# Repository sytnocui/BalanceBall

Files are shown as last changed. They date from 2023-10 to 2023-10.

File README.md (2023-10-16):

# 平衡立方体的球形版

**BalanceBall**

——by sytnocui 2023/8/31 v1.0

b站视频链接： TODO

## 0. 悲催往事

如果你打过**2021年的电赛**，你一定知道元器件清单里有一项是**亚克力球**，当时所有人都猜题目是球型机器人，一时间B站遍地都是球形机器人的视频，我们也为此屯了一堆的亚克力球，为了买球少说就花了200块钱。但可能因为疫情推迟比赛等原因，最后控制题却是一个和亚克力球毫无关系的医院物流小车。在我们破大防的同时，那一堆亚克力球怎么处理就成了问题。

>   亚克力球滞销，救救我们！！！
>

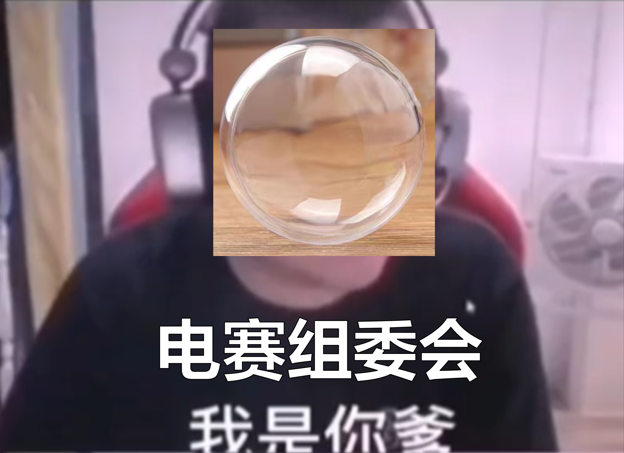
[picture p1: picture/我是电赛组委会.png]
我是电赛组委会


## 1. 项目说明

本项目旨在做出**球形版的平衡立方体**。在总体架构上，使用三个无刷电机带动三个正交安装的飞轮，并将整个球至于由三个**全向轮**构成的底盘上。全向轮允许前进方向和轴向的运动，则三个全向轮构成的底盘即可允许平衡球在上面做**三自由度全姿态自由机动**。球在全向轮底盘上，利用角动量守恒的原理实现球在底盘上的全姿态自由机动。

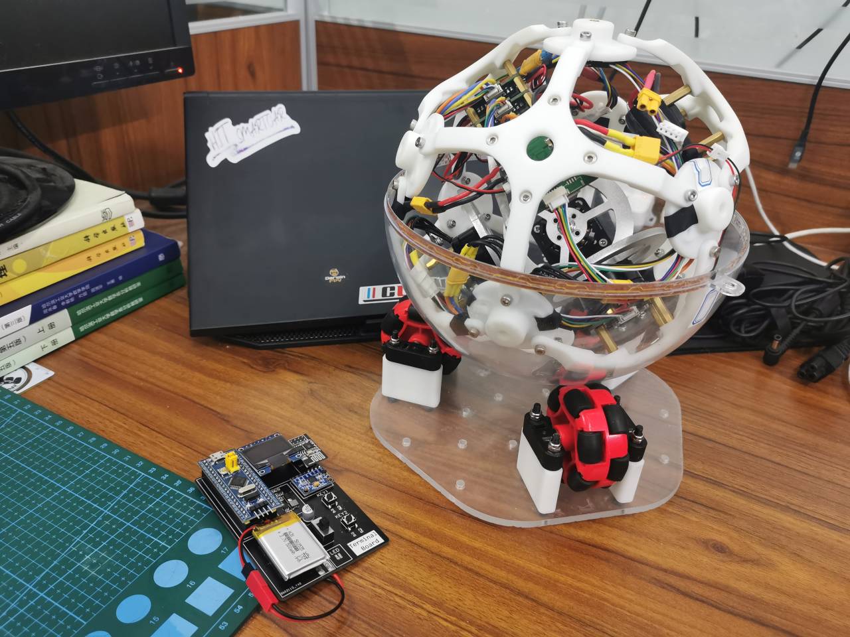
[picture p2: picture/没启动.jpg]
没启动


再贴张solidworks爆炸渲染图~

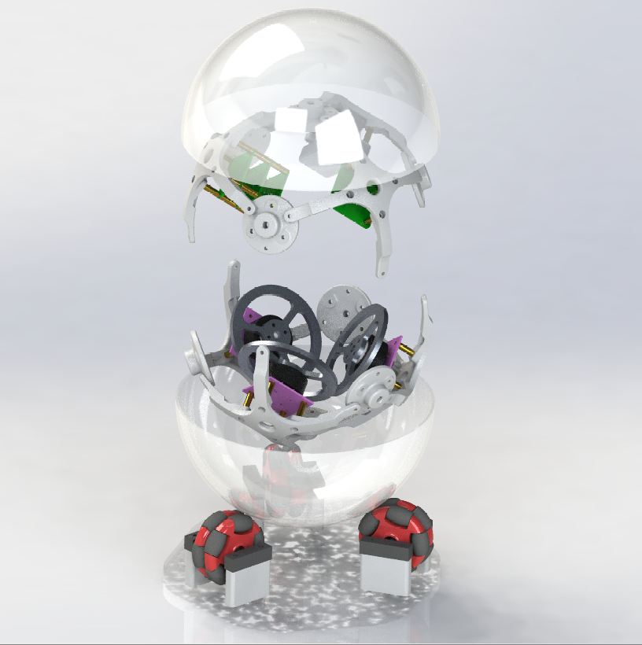
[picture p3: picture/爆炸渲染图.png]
爆炸渲染图


## 2. 开源协议

本项目使用 Apache 2.0 开源协议，转载请标明出处

## 3. 项目属性

本项目为首次公开，为本人原创项目。项目未曾在别的比赛中获奖。

另外，本项目同时也是我大四的大创项目，目前还未结题，之后会不会传给学弟去报竞赛还待商榷。

## 4. 项目相关功能及实物展示

-   平衡球全姿态自由转动

-   平衡球三轴角速度闭环控制与助力模式

-   平衡球三轴姿态跟踪随动，需搭配终端完成

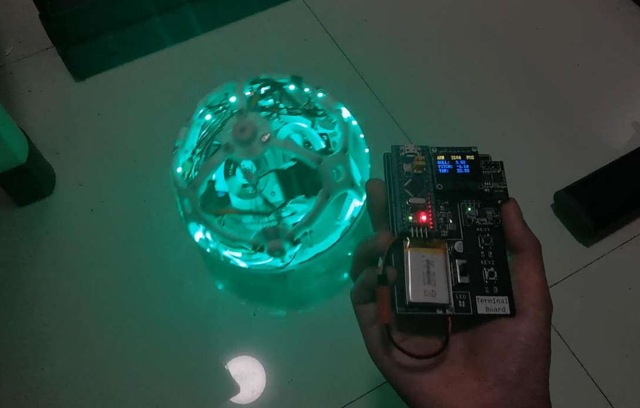
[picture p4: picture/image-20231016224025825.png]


-   平衡球实时发布自身三轴姿态，可模仿流浪地球方向盘，用于游玩各种赛车游戏

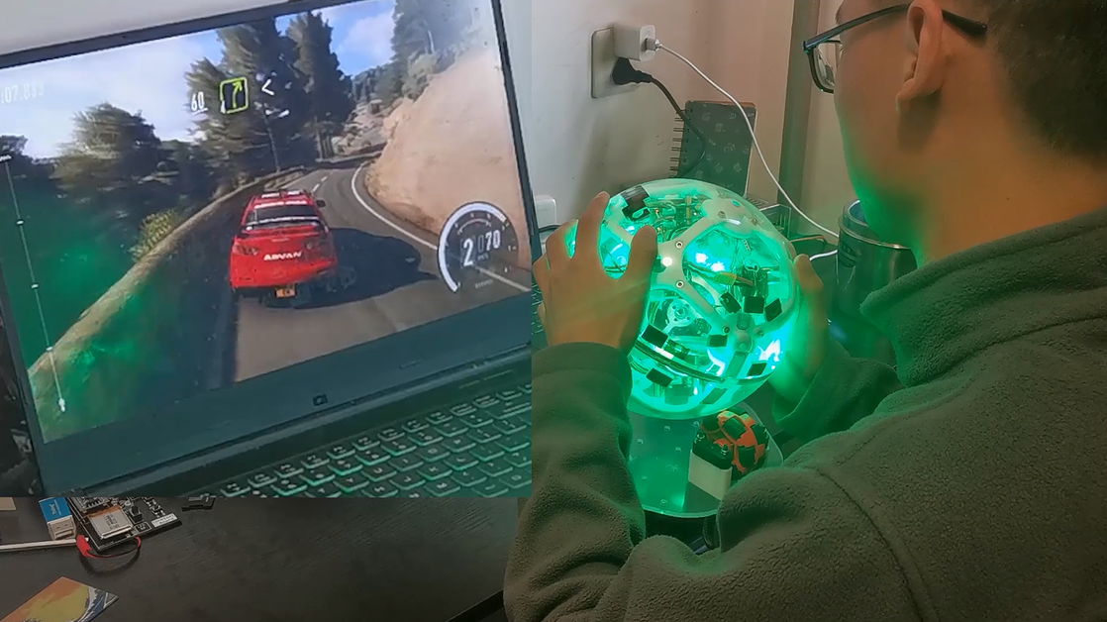
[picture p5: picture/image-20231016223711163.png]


## 5. 设计原理

项目总体可分为结构设计，硬件设计，软件设计三部分

### 5.1 结构设计

项目的结构设计理念很大程度上参考了苏黎世的经典平衡立方体：

平衡立方体视频

依照上图，平衡立方体有六个面，按照离地面的远近关系，咱们可以分成上三面和下三面。可以很明显得看到，平衡立方体的三个正交飞轮安装在下三面，而电池、电路板等均安装在上三面。

根据立体几何原理，可以很顺理成章地想到正方体是有外接球的。**取平衡立方体的外接球，将其六个面全部向外投影到其外接球上，就是咱们的平衡球**。

依据此建立的3D模型如下：

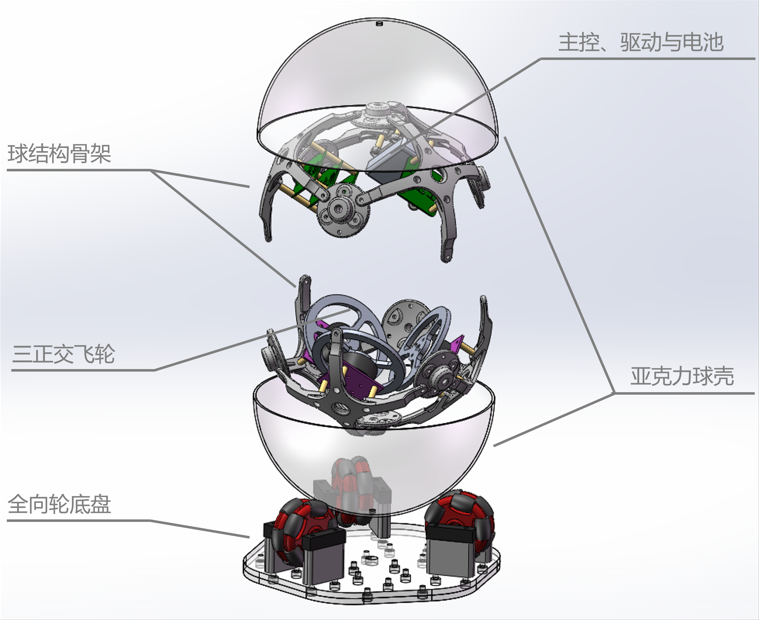
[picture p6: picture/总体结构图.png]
总体结构图


### 5.2 硬件设计

本项目设计有主控板，FOC驱动板，编码器板与陀螺仪板。项目硬件拓扑图如下：

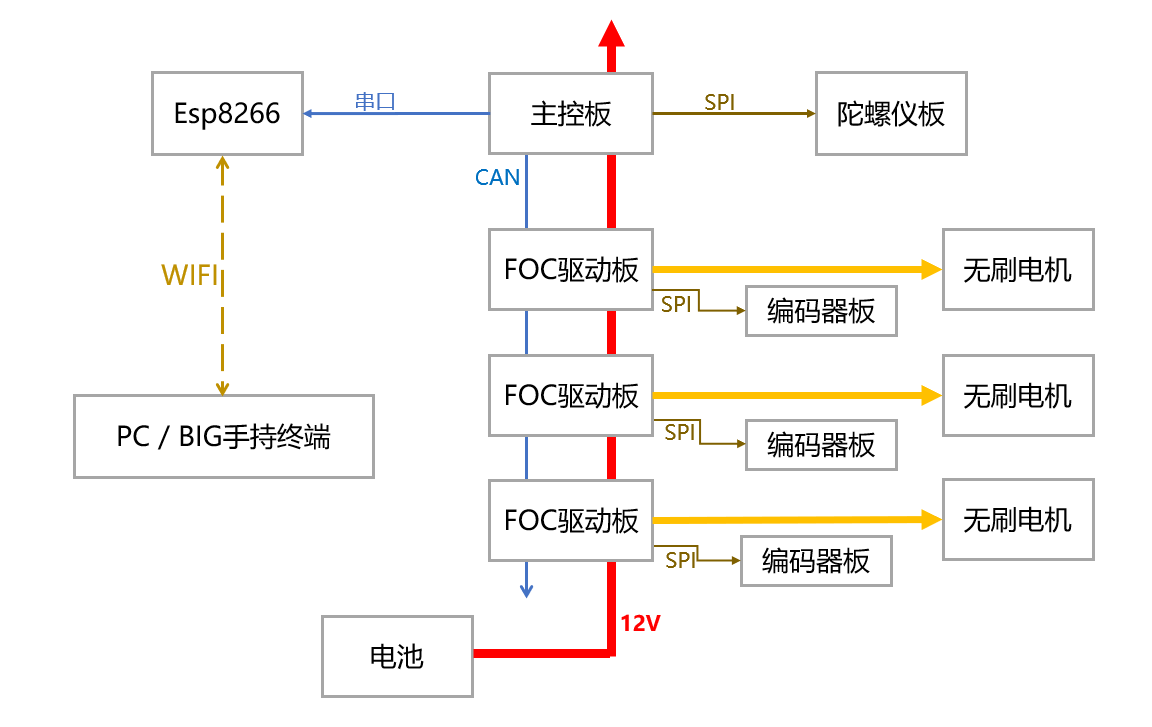
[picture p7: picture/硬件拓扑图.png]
硬件拓扑图


其中：

-   主控板和FOC驱动板全部采用级联方式供电，也通过CAN总线级联传递目标指令。
-   共三个FOC驱动板，每个FOC驱动板均连接一个编码器板获取无刷电机位置，并驱动一个无刷电机。
-   主控板连接有一块陀螺仪板，实时读取姿态信息。
-   主控板连接有一块esp8266通信模块

#### 5.2.1 主控板

主控板为四层板，可嘉立创免费打印。主要完成WIFI无线通信，读取陀螺仪姿态，姿态解算，控制模式管理，控制算法运行等。

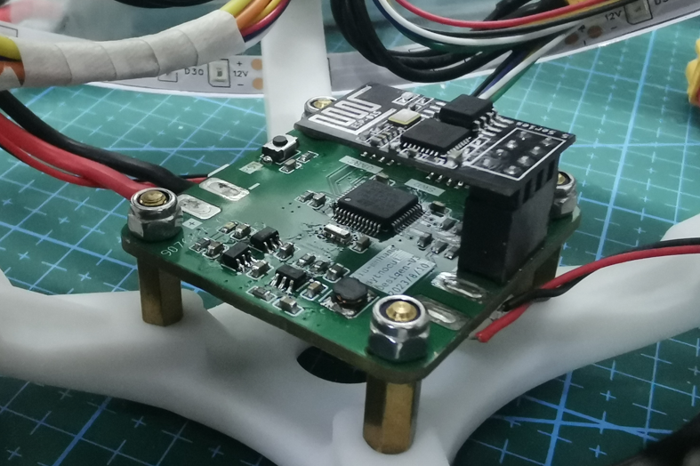
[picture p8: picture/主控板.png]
主控板


-   主控：STM32F103C8T6
-   晶振： 村田陶瓷三脚晶振CSTCE 8M （**稚晖君机械臂同款，不需要接负载电容**）

-   CAN通讯芯片：TJA1050T（**注意需5V供电，否则单片机CAN收发会卡死**）

-   电源管理：JW5026+ME6211
-   无线通信：经典插针式Esp8266无线通信模块

-   所用排座皆为GH1.25型号；

>   某宝上均可以买到，估测成本价一套下来大致30rmb左右（电子元件价格可能会有变化）。

配套编码器板可为：ICM20602，MPU6050，*ICM42688P（暂有问题，发热严重，请用icm20602模块代替）*

注意：编码器板使用热熔胶固定在球的内部最顶点，与地面平行。

#### 5.2.2 驱动板

驱动板为四层板，可嘉立创免费打印。驱动板主要完成FOC速度闭环驱动。

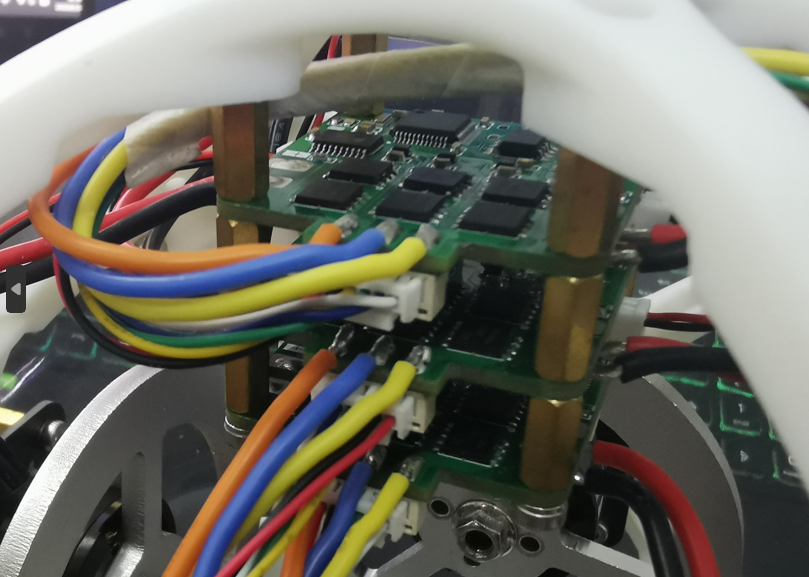
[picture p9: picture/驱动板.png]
驱动板


驱动板设计参考了柠檬FOC开源板，基于GD32进行设计。

参考地址： [【新春快乐】柠檬FOC开源板 - 嘉立创EDA开源硬件平台 (oshwhub.com)](https://oshwhub.com/a1804889557/xin-chun-kuai-le-ning-meng-FOCka) 

驱动板硬件部分自主设计，软件部分直接烧录柠檬FOC的代码使用。原开源项目可以通过putty串口助手设置电流闭环，速度和位置闭环模式，由于项目需要这里采用了速度阶跃变化模式。

使用原固件时注意在串口调试助手中修改电源欠压保护和速度保护参数，防止速度突变过快导致的电机停转。

驱动板参数如下：

-   主控：GD32C103CBT6
-   晶振： 村田陶瓷三脚晶振CSTCE 8M

-   CAN通讯芯片：SN65HVD232D

-   电源管理：JW5026+RT9013-3.3

-   电机驱动芯片：FD6288T （电机驱动芯片+mos管，大电流方案）

-   NMOS：TPH1R403NL

-   电流采样：LMV358IPWRG4 偏置低采

-   采样电阻：1206 1mR

-   所用排座皆为GH1.25型号

-   配套编码器：MT6816（**需要买支持SPI模式的**，很容易买错，不要买错了）

>   某宝上均可以买到，估测成本价一套下来大致60rmb左右（电子元件价格可能会有变化）。

#### 5.3.3 BIG手持终端

BIG手持终端是两层板，可嘉立创免费打印。BIG手持终端主要完成远程改变控制模式，安全管理，实时状态显示，发布目标位姿等功能。

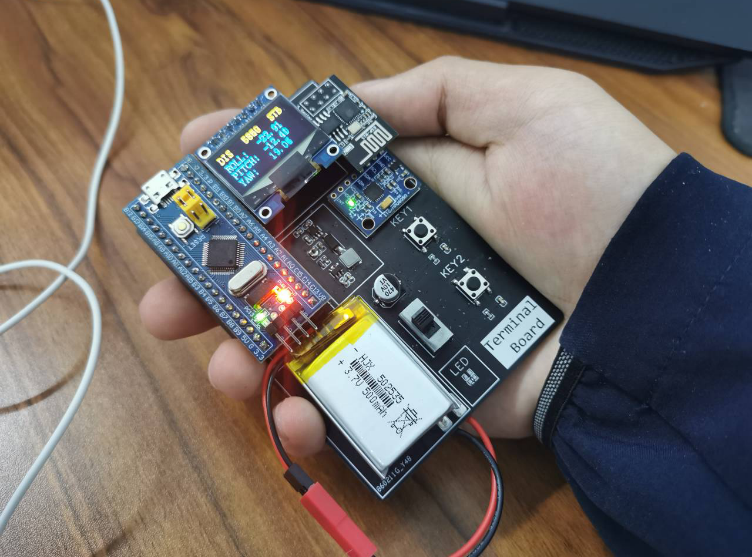
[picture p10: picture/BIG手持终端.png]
BIG手持终端


该模块对标稚晖君的PICO小终端设计，主要完成一些人机交互的功能。因为面向初学者，所有看起来比较粗野。因为PICO是微小的意思，稚晖君的PICO确实很小，但我这个手持终端却很大，所以起名叫**BIG**。

手持终端参数如下：

-   主控：STM32F103C8T6蓝宝石核心板
-   显示：7脚OLED显示屏，SPI模式

-   电池：1s锂电池 300mah 

-   陀螺仪：经典MPU6050模块

-   无线通信：经典插针式Esp8266无线通信模块

### 5.3 软件设计

#### 5.3.1 全姿态阻力效果

在主控板上进行，利用Mahony姿态解算方法，解出实时roll pitch yaw三轴角度，并分别建立PID反馈控制。每当有某个轴上有角速度，通过PID算法在该轴上产生相反方向的控制输出。最终将三轴的PID控制输出叠加后，左乘转速分配矩阵，将其解算成三个正交安装的飞轮的转速，输出给FOC驱动板，即可在球的三自由度全姿态运动中产生阻力效果。

#### 5.3.2 三轴姿态跟踪随动

在5.3.1节的基础上，添加姿态角反馈，由BIG手持终端收集自身姿态，作为平衡球姿态的目标值，与平衡球姿态的实际值做差，构成PID控制器。最终实现三轴姿态跟踪随动。

因为全向轮底盘会给系统引入非常大的摩擦力，所以目前这个功能需要将球直接放在地面上，而不能放在全向轮底盘上进行。

考虑到纯PID效果有限，本项目之后会使用LQR等控制算法部署上做进一步对比测试。

#### 5.3.3 作为方向盘游玩赛车游戏

我们偶然发现，我们的球和流浪地球的球形方向盘非常类似，于是，使用wifi模块连接电脑，接收球形仿真器实时姿态信息，并将其使用python的vgamepad库，映射成虚拟的xbox游戏手柄的摇杆值（方向盘，油门，刹车等）。这样就可以在尘埃拉力赛2.0等赛车游戏中识别虚拟游戏摇杆，进而获得控制数据了。

因为是将控制数据封装成xbox手柄的形式，所以不管游玩任何赛车游戏，都不会有兼容性的问题。

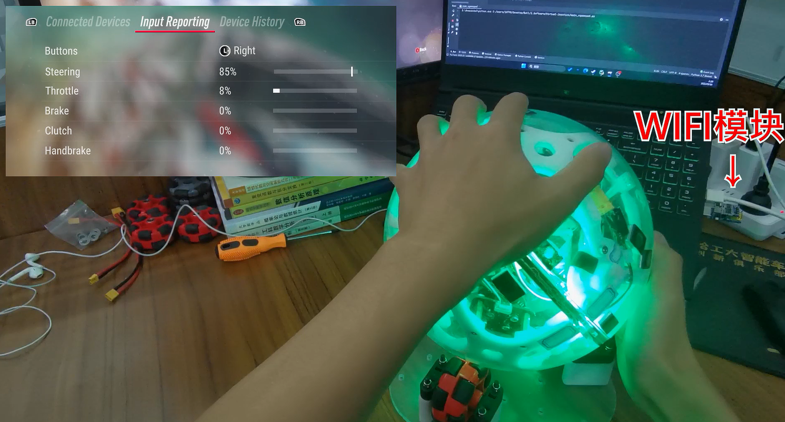
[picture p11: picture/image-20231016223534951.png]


## 6. 注意事项

### 6.1 软件说明

本项目提供主控板与BIG手持终端的固件代码，驱动板的固件与柠檬FOC完全一致，烧录与使用也请完全参考柠檬FOC的工程：

参考链接： [【新春快乐】柠檬FOC开源板 - 嘉立创EDA开源硬件平台 (oshwhub.com)](https://oshwhub.com/a1804889557/xin-chun-kuai-le-ning-meng-FOCka) 

本项目所有单片机固件均使用Clion开发，如果你对Clion工程配置比较生疏，建议观看稚晖君的Clion+Stm32环境配置指南：

参考链接： [配置CLion用于STM32开发【优雅の嵌入式开发】 - 知乎 (zhihu.com)](https://zhuanlan.zhihu.com/p/145801160) 

### 6.2 电机选型

飞轮与无刷电机的选型是十分重要的，由于整个系统摩擦力很大，开源社区常见的莱洛三角形和平衡方块使用的低kv云台电机很难满足力矩需求。我在淘宝二手电机无意中发现了这款电机：

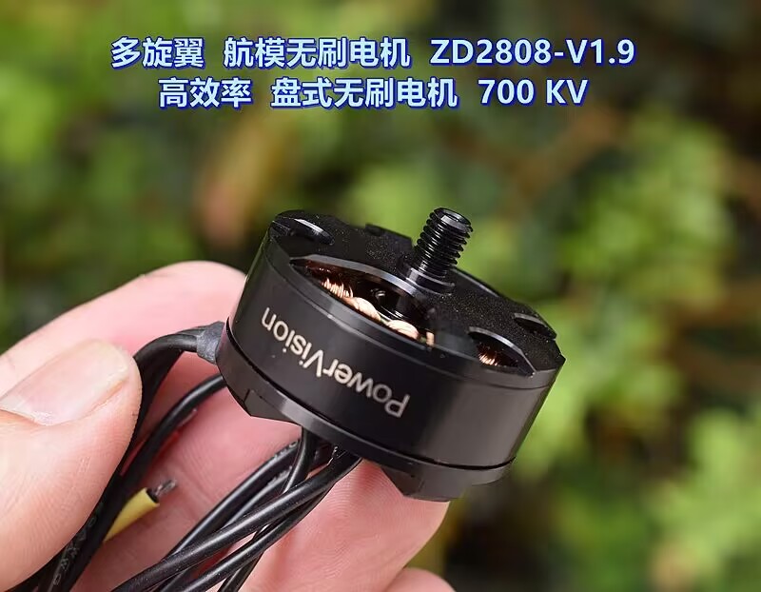
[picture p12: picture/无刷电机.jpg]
无刷电机


经过测试，该电机负载能力用到本项目非常合适，成本低廉（仅16元），且比较节省空间。考虑到这种二手电机经常卖完就没了，如果之后该电机售罄，可以考虑使用 *大疆2312精灵电机* 替代。

另外，若铝合金飞轮可以提供的反作用力矩不足，可模仿这个开源工程的方案，自制飞轮并在外边缘钻孔安装螺栓来增加飞轮转动惯量。

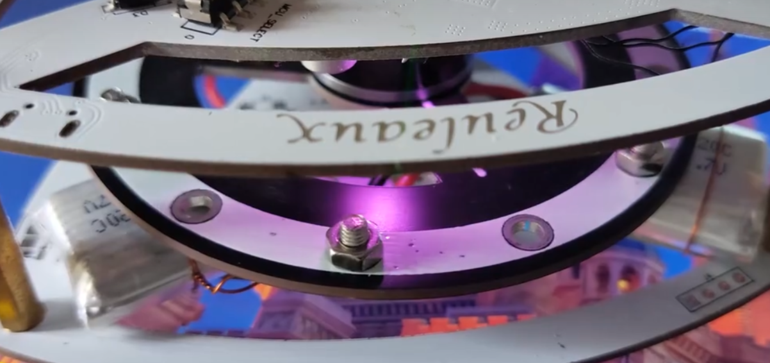
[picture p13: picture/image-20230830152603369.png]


参考地址：[基于LQR控制器的自平衡莱洛三角形_哔哩哔哩_bilibili](https://www.bilibili.com/video/BV19v411n7mN/?vd_source=4ff5d8b280178b24895437b1b8ffd97e) 

### 6.3 陀螺仪选型

本项目涉及的陀螺仪板使用的是icm42688p，但是从某宝买的不同批次的icm42688p均出现虽然能读出正确的数据，但有发热严重（约60度），带来的温漂严重等问题。确认不是焊接问题，暂时不知道是不是物料问题或者硬件设计有问题。建议谨慎考虑从淘宝购买icm42688p。本项目暂时使用逐飞科技的icm20602模块充当陀螺仪板。

本项目目前使用的是从社团嫖的icm20602模块，同时球主控板也支持mpu6050接插件。三款陀螺仪的驱动代码均在工程中，但接口代码需自行更改。

## 8. 项目进度

**2023/8/30首次开源**

项目已完成的部分：

-   项目已完成所有结构+硬件设计与搭建，结构与硬件设计已经收敛成熟。
-   项目已完成所有逻辑代码编写。
-   项目已完成基础的控制算法的编写，可以完成基础的角速度闭环与姿态闭环控制。

项目的后续计划：

-   由于控制系统的复杂性，项目后续需要对姿态闭环控制代码做优化，主要措施包括：
    -   增加配重，使重心趋于球形正中心，且使三轴惯量趋于一致。
    -   PID是真不行，换成基于模型的控制算法，如基于欧拉方程基于LQR建模
    -   对摩擦力进行参数辨识，使用干扰观测器补偿之（也可使用ADRC算法）
    -   尝试基于四元数的姿态闭环控制，以消除欧拉角死锁问题。
-   项目成员正在自主研发基于stm32f103c8t6的FOC驱动代码。研发完成后将会替换掉目前使用的柠檬FOC大佬的基于gd32的驱动板。
-   将会基于Qt与OpenGL写一个能实时可视化姿态与远程调参的上位机软件，效果可参考稚晖君的电子机器人和各种飞控调试助手。
-   将会实现一套嵌入式shell，以支持通过wifi串口进行远程调参
-   为陀螺仪添加减震垫，防止电机的高频振动给陀螺仪引入干扰
-   找出icm42688p的问题，换掉现在正在用的icm20602

## 9. 物资说明

结构件物料清单：

| 物资 | 用途 | 需求个数 | 购买链接 |
| :--- | --- | :---: | --- |
| **球主体结构** | | | |
| 亚克力球壳 20mm | 球透明外壳 | >=2 | https://m.tb.cn/h.54hODsa?tk=Q7ZXdzW9Ydo |
| 3D打印（内部支撑架-连点） | 十字形主体框架 | 6 | 嘉立创三维猴 |
| 3D打印（内部支撑架-桥接点） | 主体框架的连接点 | 8 | 嘉立创三维猴 |
| 3D打印（支架-电池小） | 固定电池 | 1 | 嘉立创三维猴 |
| **无刷电机相关** | | | |
| 盘式无刷电机ZD2808-V1.9 | | 3 | https://m.tb.cn/h.5WJTsy4?tk=4qczdC51605 |
| 铝合金飞轮6mm 80mm | | 3 | https://m.tb.cn/h.5e1xS1N?tk=HlGCdC6gCA1 |
| 径向磁铁6*2.5 | 获取电机轴位置 | 3 | https://m.tb.cn/h.54hiYKJ?tk=QM5mdzWTh2m |
| 3M超能胶 | 将磁体固定在电机轴上 | 1 | https://m.tb.cn/h.54AlcCb?tk=jlEVdzWQEFG |
| **球主体配件** | | | |
| M3*8杯头螺丝 | 主要结构固定螺丝 | 若干 | |
| M3防松螺母 | 主要结构固定螺母 | 若干 | |
| 铜柱 M3*10+6 | 主要支撑铜柱 | 20 | |
| M3*5\*5嵌入式螺母 | 连接球壳与3D打印件 | 2 | |
| M3*8沉头螺丝 | 连接球壳与3D打印件 | 2 | |
| 配重 | 平衡重心位置 | 若干 | https://m.tb.cn/h.56VXPSI?tk=n4DUWYhMTac |
| **电路部分** | | | |
| 主控板 | | 1 | 嘉立创免费打板，元件自行处理 |
| FOC驱动板 | | 3 | 嘉立创免费打板，元件自行处理 |
| 编码器板 | | 3 | 嘉立创免费打板，元件自行处理 |
| 陀螺仪板（可选） | | 1 | 嘉立创免费打板，元件自行处理 |
| BIG手持终端 | | 1 | 嘉立创免费打板，元件自行处理 |
| wifi模块 | 球与BIG，球与PC通信  | 3 | https://m.tb.cn/h.56vZKps?tk=XmldWYhGjPn |
| wifi模块连接电脑的usb转串模块 | 球与PC通信 | 1 | https://m.tb.cn/h.56vZKps?tk=XmldWYhGjPn |
| 航模电池3s 550mah 85c | 供电 | >=1 | https://m.tb.cn/h.5fuIsF0?tk=Pxn2dzWQvsg |
| **线材** | | | |
| 硅胶线18awg | 电源线 | 若干 | |
| 硅胶线20awg | 电机线 | 若干 | |
| GH1.25 6p 双头反向 30cm | 编码器线 | 3 | |
| GH1.25 6p 双头反向 30cm | 陀螺仪线 | 1 | |
| GH1.25 2p 双头反向 15cm | CAN总线 | 4 | |
| xt30头 | 连接电池 | 1 | |
| **底盘** | | | |
| 亚克力切割（底盘-上层） | 底盘主体 | 1 | 淘宝找亚克力切割 |
| 3D打印（全向轮轴座-键） | 支撑全向轮 | 3 | 嘉立创三维猴 |
| 3D打印（全向轮轴座-圆） | 支撑全向轮 | 3 | 嘉立创三维猴 |
| 3D打印（万向轮支撑腿-分体式） | 支撑全向轮 | 6 | 嘉立创三维猴 |
| F车模全向轮 | 支撑亚克力球壳 | 3 | https://m.tb.cn/h.5Vqiebu?tk=y4CAdzW76o4 |
| 轴承7\*11\*3 | 连接全向轮和光轴 | 6 | https://m.tb.cn/h.54hQEqA?tk=cFWBdzW7L1a |
| 光轴切割（全向轮光轴） | 支撑全向轮，注意开槽 | 3 | https://m.tb.cn/h.5fuKVfU?tk=G4sGdzW7mtl |
| M4*55螺丝 | 固定全向轮轴座 | 12 | |
| M4防松螺母 | 固定全向轮轴座 | 12 | |
| 脚垫（可选） | 底座防滑 | 若干 | https://m.tb.cn/h.54AknHL?tk=cSfIdzWjeUe |

整套下来价格800~1000元左右，某些零部件价格变化较大，请以实际情况为准。

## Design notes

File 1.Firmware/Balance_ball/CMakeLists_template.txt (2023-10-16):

#THIS FILE IS AUTO GENERATED FROM THE TEMPLATE! DO NOT CHANGE!
set(CMAKE_SYSTEM_NAME Generic)
set(CMAKE_SYSTEM_VERSION 1)
cmake_minimum_required(VERSION 3.17)

# specify cross compilers and tools
set(CMAKE_C_COMPILER arm-none-eabi-gcc)
set(CMAKE_CXX_COMPILER arm-none-eabi-g++)
set(CMAKE_ASM_COMPILER  arm-none-eabi-gcc)
set(CMAKE_AR arm-none-eabi-ar)
set(CMAKE_OBJCOPY arm-none-eabi-objcopy)
set(CMAKE_OBJDUMP arm-none-eabi-objdump)
set(SIZE arm-none-eabi-size)
set(CMAKE_TRY_COMPILE_TARGET_TYPE STATIC_LIBRARY)

# project settings
project(BalanceBall C CXX ASM)
set(CMAKE_CXX_STANDARD 17)
set(CMAKE_C_STANDARD 11)

#Uncomment for hardware floating point
#add_compile_definitions(ARM_MATH_CM4;ARM_MATH_MATRIX_CHECK;ARM_MATH_ROUNDING)
#add_compile_options(-mfloat-abi=hard -mfpu=fpv4-sp-d16)
#add_link_options(-mfloat-abi=hard -mfpu=fpv4-sp-d16)

#Uncomment for software floating point
#add_compile_options(-mfloat-abi=soft)

add_compile_options(-mcpu=cortex-m3 -mthumb -mthumb-interwork)
add_compile_options(-ffunction-sections -fdata-sections -fno-common -fmessage-length=0)

# uncomment to mitigate c++17 absolute addresses warnings
#set(CMAKE_CXX_FLAGS "${CMAKE_CXX_FLAGS} -Wno-register")

if ("${CMAKE_BUILD_TYPE}" STREQUAL "Release")
    message(STATUS "Maximum optimization for speed")
    add_compile_options(-Ofast)
elseif ("${CMAKE_BUILD_TYPE}" STREQUAL "RelWithDebInfo")
    message(STATUS "Maximum optimization for speed, debug info included")
    add_compile_options(-Ofast -g)
elseif ("${CMAKE_BUILD_TYPE}" STREQUAL "MinSizeRel")
    message(STATUS "Maximum optimization for size")
    add_compile_options(-Os)
else ()
    message(STATUS "Minimal optimization, debug info included")
    add_compile_options(-Og -g)
endif ()

include_directories(
        Core/Inc
        USB_DEVICE/App
        USB_DEVICE/Target
        Drivers/STM32F1xx_HAL_Driver/Inc
        Drivers/STM32F1xx_HAL_Driver/Inc/Legacy
        Middlewares/ST/STM32_USB_Device_Library/Core/Inc
        Middlewares/ST/STM32_USB_Device_Library/Class/CDC/Inc
        Drivers/CMSIS/Device/ST/STM32F1xx/Include
        Drivers/CMSIS/Include
        Bsp
        Ctrl
        UserApp
)

add_definitions(-DUSE_HAL_DRIVER -DSTM32F103xB)

file(GLOB_RECURSE SOURCES
        "startup/*.*"
        "Middlewares/*.*"
        "Drivers/*.*"
        "USB_DEVICE/*.*"
        "Core/*.*"
        "Ctrl/*.*"
        "Bsp/*.*"
        "UserApp/*.*"
        )

set(LINKER_SCRIPT ${CMAKE_SOURCE_DIR}/STM32F103C8Tx_FLASH.ld)

add_link_options(-Wl,-gc-sections,--print-memory-usage,-Map=${PROJECT_BINARY_DIR}/${PROJECT_NAME}.map)
add_link_options(-mcpu=cortex-m3 -mthumb -mthumb-interwork)
add_link_options(-T ${LINKER_SCRIPT})

add_executable(${PROJECT_NAME}.elf ${SOURCES} ${LINKER_SCRIPT})

set(HEX_FILE ${PROJECT_BINARY_DIR}/${PROJECT_NAME}.hex)
set(BIN_FILE ${PROJECT_BINARY_DIR}/${PROJECT_NAME}.bin)

add_custom_command(TARGET ${PROJECT_NAME}.elf POST_BUILD
        COMMAND ${CMAKE_OBJCOPY} -Oihex $<TARGET_FILE:${PROJECT_NAME}.elf> ${HEX_FILE}
        COMMAND ${CMAKE_OBJCOPY} -Obinary $<TARGET_FILE:${PROJECT_NAME}.elf> ${BIN_FILE}
        COMMENT "Building ${HEX_FILE}
Building ${BIN_FILE}")

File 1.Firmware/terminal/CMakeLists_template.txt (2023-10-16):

#THIS FILE IS AUTO GENERATED FROM THE TEMPLATE! DO NOT CHANGE!
set(CMAKE_SYSTEM_NAME Generic)
set(CMAKE_SYSTEM_VERSION 1)
cmake_minimum_required(VERSION 3.17)

# specify cross compilers and tools
set(CMAKE_C_COMPILER arm-none-eabi-gcc)
set(CMAKE_CXX_COMPILER arm-none-eabi-g++)
set(CMAKE_ASM_COMPILER  arm-none-eabi-gcc)
set(CMAKE_AR arm-none-eabi-ar)
set(CMAKE_OBJCOPY arm-none-eabi-objcopy)
set(CMAKE_OBJDUMP arm-none-eabi-objdump)
set(SIZE arm-none-eabi-size)
set(CMAKE_TRY_COMPILE_TARGET_TYPE STATIC_LIBRARY)

# project settings
project(terminal C CXX ASM)
set(CMAKE_CXX_STANDARD 17)
set(CMAKE_C_STANDARD 11)

#Uncomment for hardware floating point
#add_compile_definitions(ARM_MATH_CM4;ARM_MATH_MATRIX_CHECK;ARM_MATH_ROUNDING)
#add_compile_options(-mfloat-abi=hard -mfpu=fpv4-sp-d16)
#add_link_options(-mfloat-abi=hard -mfpu=fpv4-sp-d16)

#Uncomment for software floating point
#add_compile_options(-mfloat-abi=soft)

add_compile_options(-mcpu=cortex-m3 -mthumb -mthumb-interwork)
add_compile_options(-ffunction-sections -fdata-sections -fno-common -fmessage-length=0)

# uncomment to mitigate c++17 absolute addresses warnings
#set(CMAKE_CXX_FLAGS "${CMAKE_CXX_FLAGS} -Wno-register")

if ("${CMAKE_BUILD_TYPE}" STREQUAL "Release")
    message(STATUS "Maximum optimization for speed")
    add_compile_options(-Ofast)
elseif ("${CMAKE_BUILD_TYPE}" STREQUAL "RelWithDebInfo")
    message(STATUS "Maximum optimization for speed, debug info included")
    add_compile_options(-Ofast -g)
elseif ("${CMAKE_BUILD_TYPE}" STREQUAL "MinSizeRel")
    message(STATUS "Maximum optimization for size")
    add_compile_options(-Os)
else ()
    message(STATUS "Minimal optimization, debug info included")
    add_compile_options(-Og -g)
endif ()

include_directories(
        Core/Inc
        Drivers/STM32F1xx_HAL_Driver/Inc
        Drivers/STM32F1xx_HAL_Driver/Inc/Legacy
        Drivers/CMSIS/Device/ST/STM32F1xx/Include
        Drivers/CMSIS/Include
        Middlewares/ST/STM32_USB_Device_Library/Core/Inc
        Middlewares/ST/STM32_USB_Device_Library/Class/CDC/Inc
        USB_DEVICE/App
        USB_DEVICE/Target/
        Bsp
        UserApp
        Ctrl
)

add_definitions(-DUSE_HAL_DRIVER -DSTM32F103xB)

file(GLOB_RECURSE SOURCES "startup/*.*" "Drivers/*.*" "Core/*.*" "Bsp/*.*" "UserApp/*.*" "USB_DEVICE/*.*" "Middlewares/*.*"
        "Ctrl/*.*")

set(LINKER_SCRIPT ${CMAKE_SOURCE_DIR}/STM32F103C8Tx_FLASH.ld)

add_link_options(-Wl,-gc-sections,--print-memory-usage,-Map=${PROJECT_BINARY_DIR}/${PROJECT_NAME}.map)
add_link_options(-mcpu=cortex-m3 -mthumb -mthumb-interwork)
add_link_options(-T ${LINKER_SCRIPT})

add_executable(${PROJECT_NAME}.elf ${SOURCES} ${LINKER_SCRIPT})

set(HEX_FILE ${PROJECT_BINARY_DIR}/${PROJECT_NAME}.hex)
set(BIN_FILE ${PROJECT_BINARY_DIR}/${PROJECT_NAME}.bin)

add_custom_command(TARGET ${PROJECT_NAME}.elf POST_BUILD
        COMMAND ${CMAKE_OBJCOPY} -Oihex $<TARGET_FILE:${PROJECT_NAME}.elf> ${HEX_FILE}
        COMMAND ${CMAKE_OBJCOPY} -Obinary $<TARGET_FILE:${PROJECT_NAME}.elf> ${BIN_FILE}
        COMMENT "Building ${HEX_FILE}
Building ${BIN_FILE}")

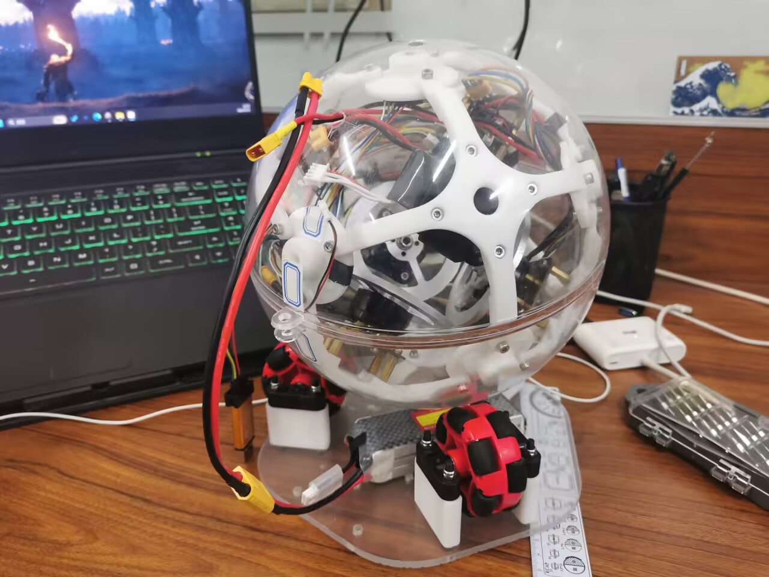
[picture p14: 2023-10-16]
picture/外接电池.jpg

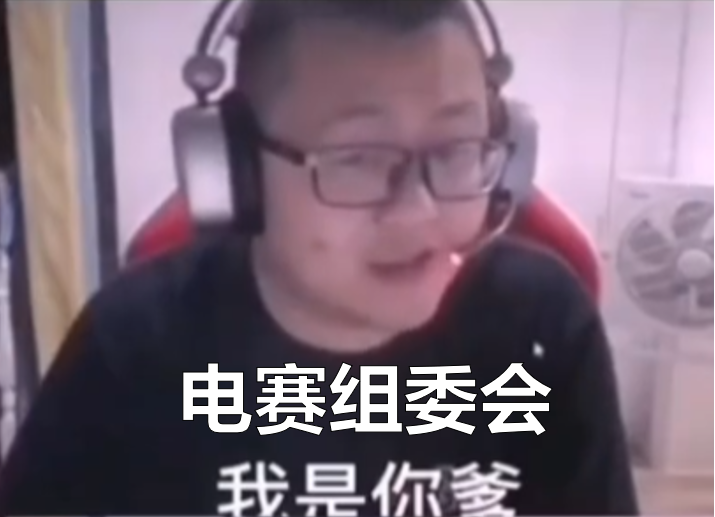
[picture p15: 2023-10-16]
picture/我是你爹.png

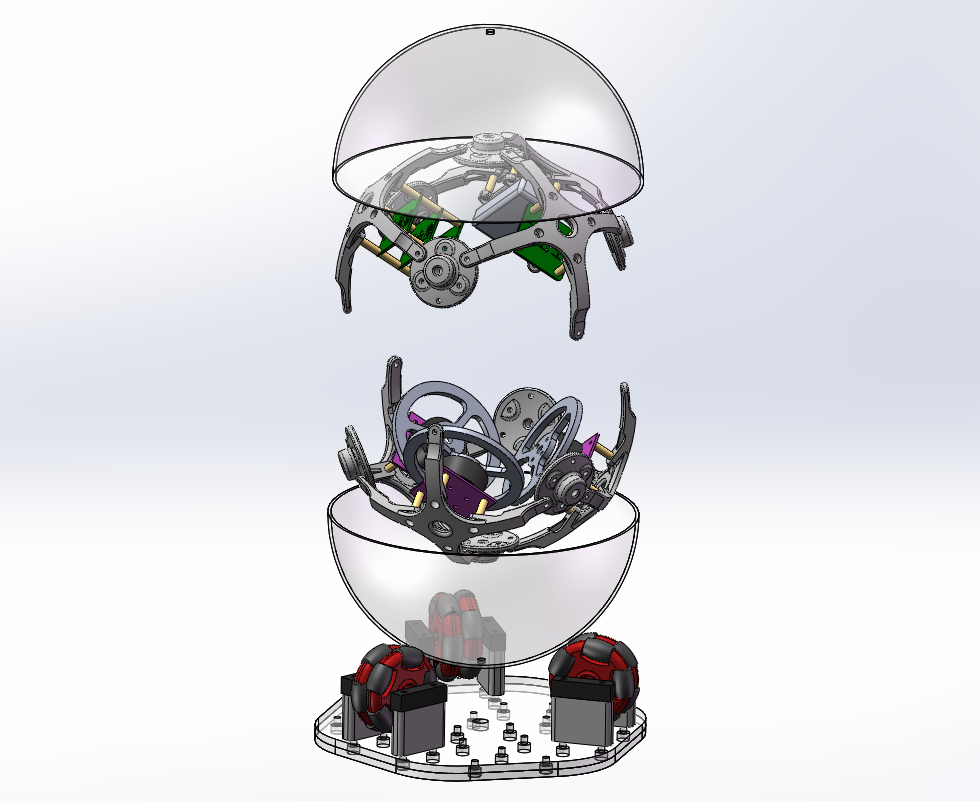
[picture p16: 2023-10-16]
picture/爆炸模型图.png

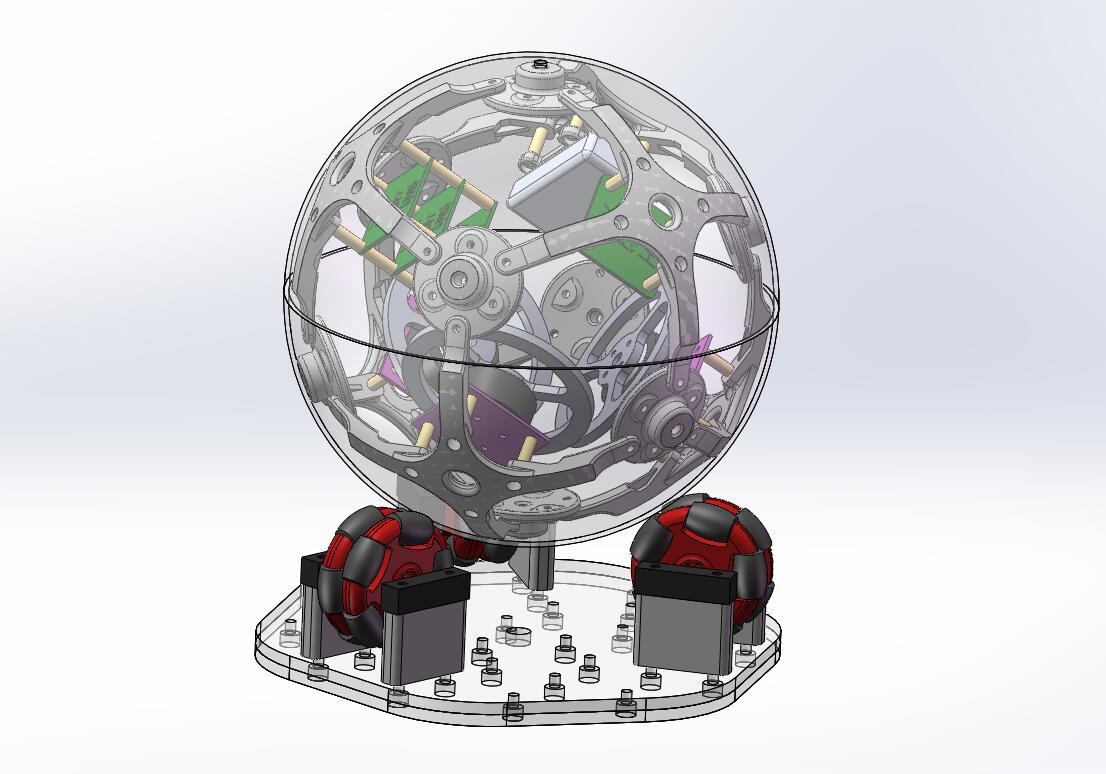
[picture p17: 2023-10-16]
picture/模型图.jpg

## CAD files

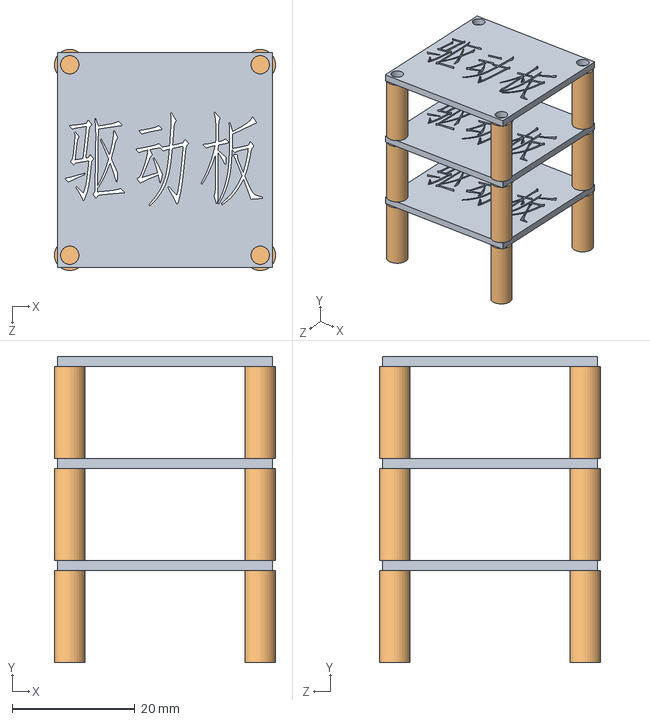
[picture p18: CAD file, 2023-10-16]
0.Model/装配体-驱动板.SLDASM
36.0 x 49.8 x 36.0 mm
驱动板 x 3
m3铜柱-主控板 x 12

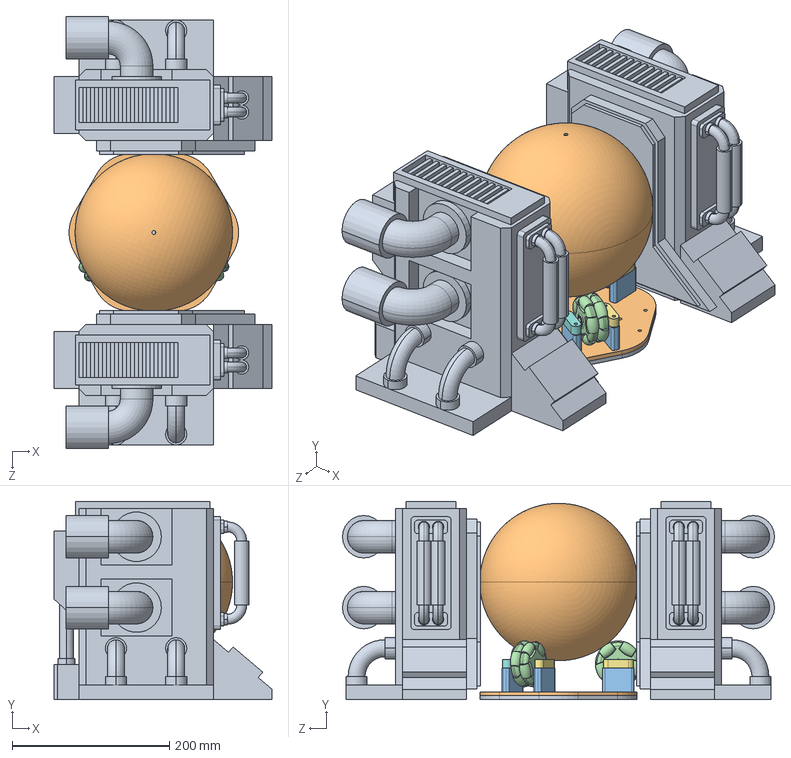
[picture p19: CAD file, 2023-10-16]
0.Model/整活/电厂装配体.SLDASM
277.0 x 252.0 x 549.0 mm
苏联电厂
底盘-上层
万向轮支撑腿-分体式 x 6
全向轮-网上找的模型58mm x 3
全向轮光轴 x 3
全向轮轴承 x 6
全向轮轴座-键 x 3
全向轮轴座-圆 x 3
底盘-下层
内部支撑架-连点 x 6
内部支撑架-桥接点 x 8
m3铜柱-4mm x 12
编码器板-AS5047P x 3
电机-2804 x 3
飞轮-80mm x 3
电机轴 x 3
m3铜柱-15mm x 12
半球壳-直径200 x 2
m3铜柱-电池 x 4
支架-电池小
电池-550mah
驱动板 x 3
m3铜柱-主控板 x 16
主控板
编码器板

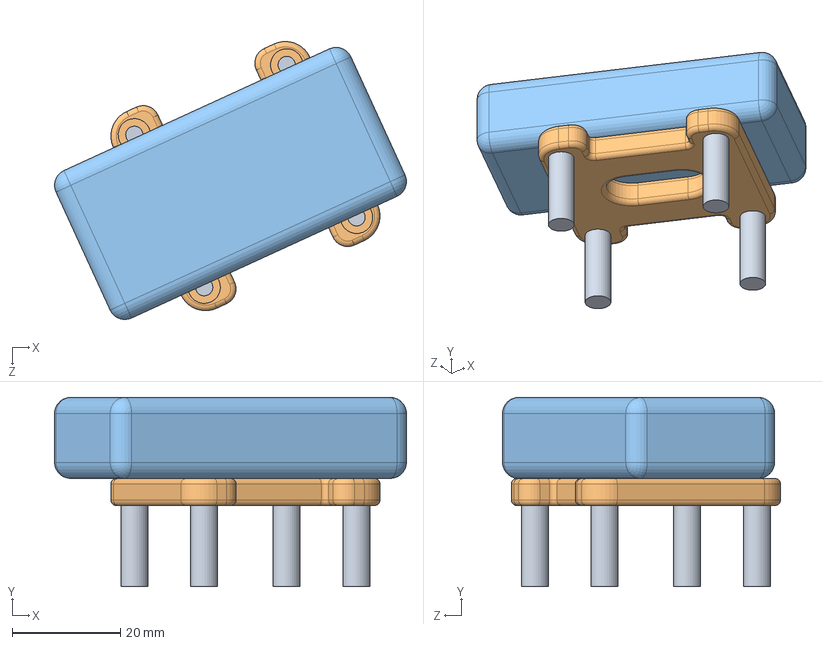
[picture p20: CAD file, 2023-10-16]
0.Model/装配体-电池.SLDASM
65.1 x 35.0 x 51.4 mm
m3铜柱-电池 x 4
支架-电池小
电池-550mah

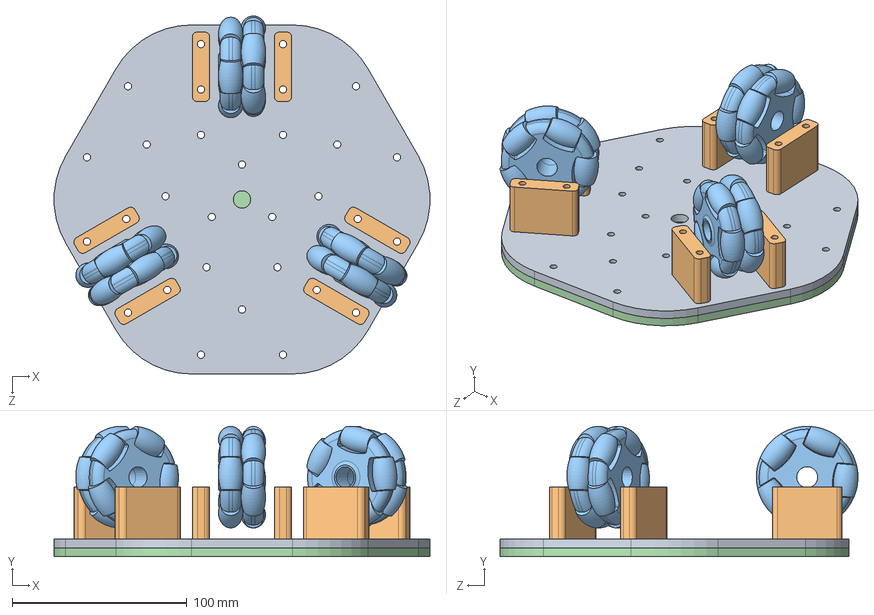
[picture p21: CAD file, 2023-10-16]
0.Model/装配体-底座.SLDASM
215.2 x 74.6 x 205.1 mm
底盘-上层
万向轮支撑腿-分体式 x 6
全向轮-网上找的模型58mm x 3
底盘-下层

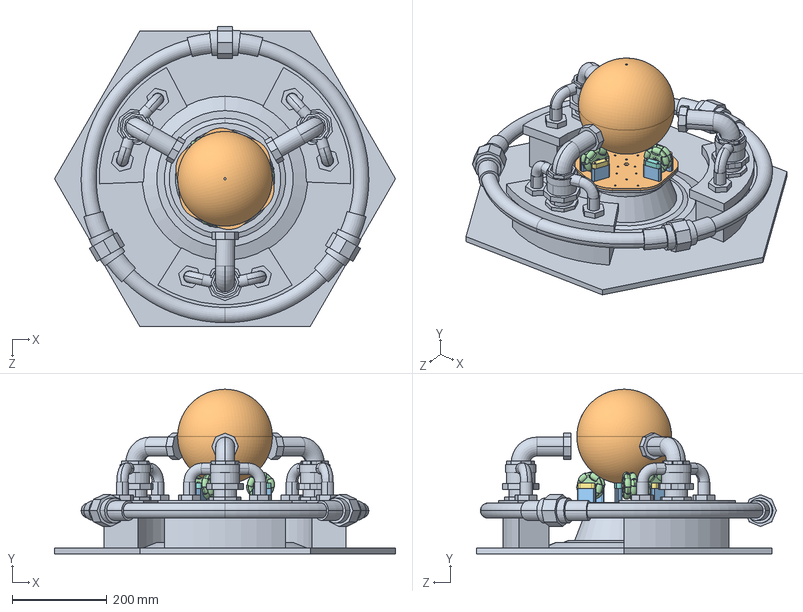
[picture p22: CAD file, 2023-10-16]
0.Model/整活/铁幕装配体.SLDASM
720.0 x 347.3 x 633.1 mm
铁幕
底盘-上层
万向轮支撑腿-分体式 x 6
全向轮-网上找的模型58mm x 3
全向轮光轴 x 3
全向轮轴承 x 6
全向轮轴座-键 x 3
全向轮轴座-圆 x 3
底盘-下层
内部支撑架-连点 x 6
内部支撑架-桥接点 x 8
m3铜柱-4mm x 12
编码器板-AS5047P x 3
电机-2804 x 3
飞轮-80mm x 3
电机轴 x 3
m3铜柱-15mm x 12
半球壳-直径200 x 2
m3铜柱-电池 x 4
支架-电池小
电池-550mah
驱动板 x 3
m3铜柱-主控板 x 16
主控板
编码器板

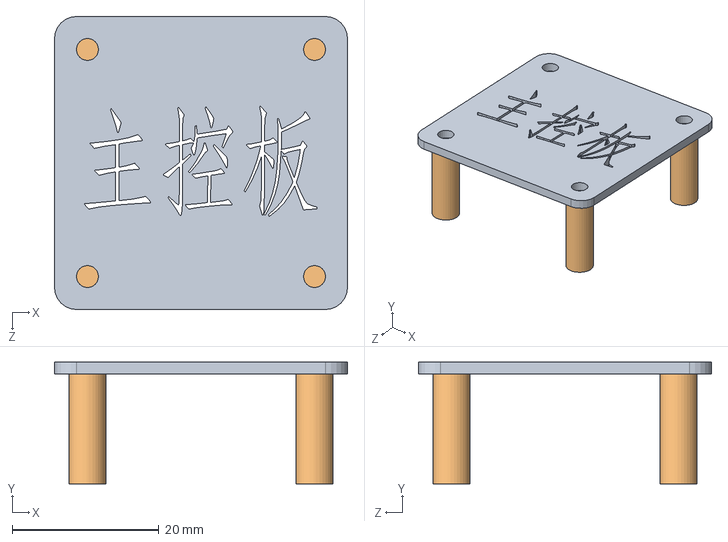
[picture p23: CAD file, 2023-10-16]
0.Model/装配体-主控板.SLDASM
40.0 x 16.6 x 40.0 mm
主控板
m3铜柱-主控板 x 4

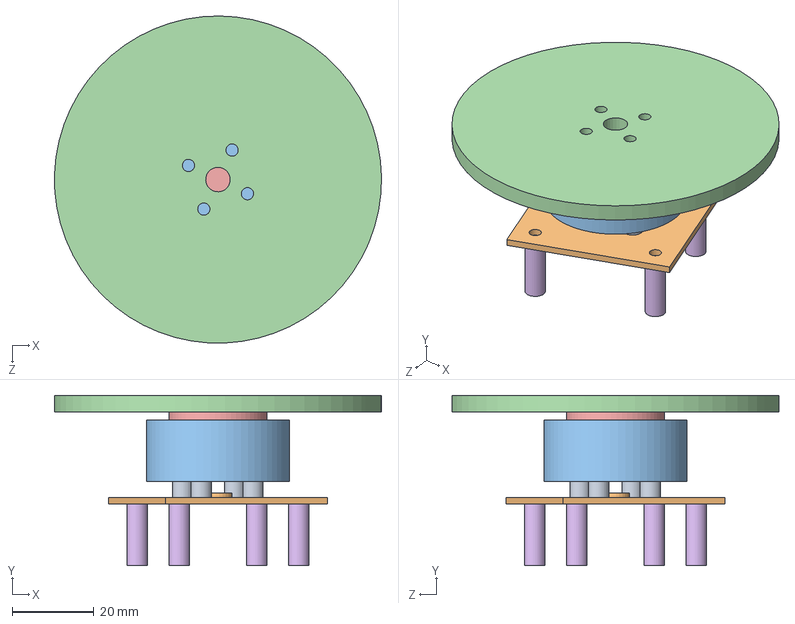
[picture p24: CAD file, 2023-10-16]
0.Model/装配体-单轴执行器.SLDASM
80.0 x 41.6 x 80.0 mm
m3铜柱-4mm x 4
编码器板-AS5047P
电机-2804
飞轮-80mm
电机轴
m3铜柱-15mm x 4

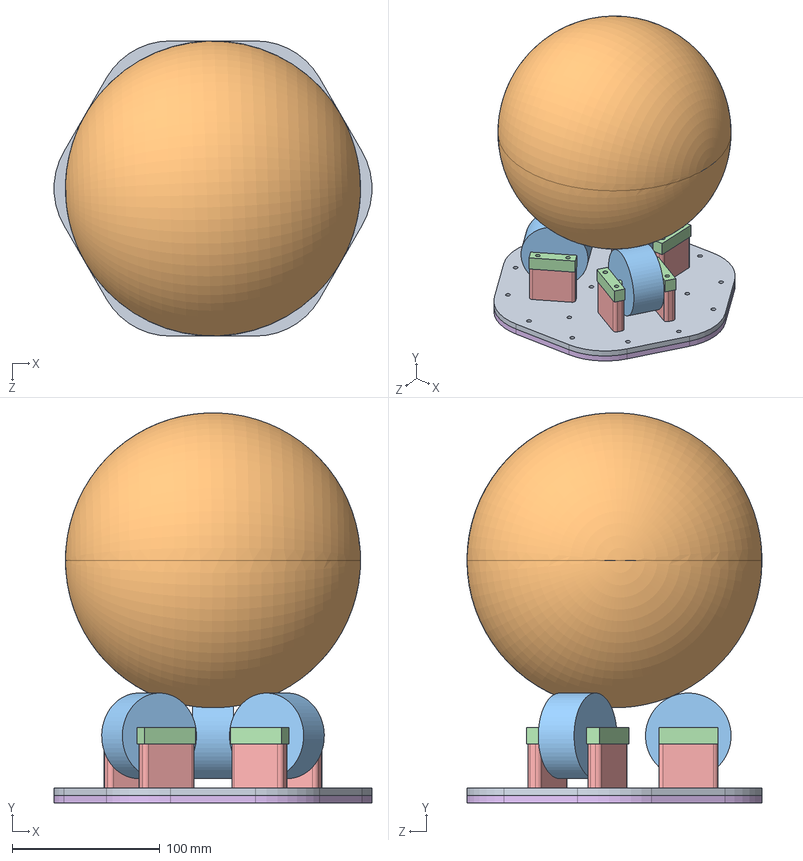
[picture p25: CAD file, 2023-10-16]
0.Model/装配体-外部.SLDASM
215.2 x 264.2 x 200.0 mm
底盘-上层
半球壳-直径200 x 2
全向轮 x 3
全向轮固定架 x 3
万向轮支撑腿-分体式 x 6
底盘-下层

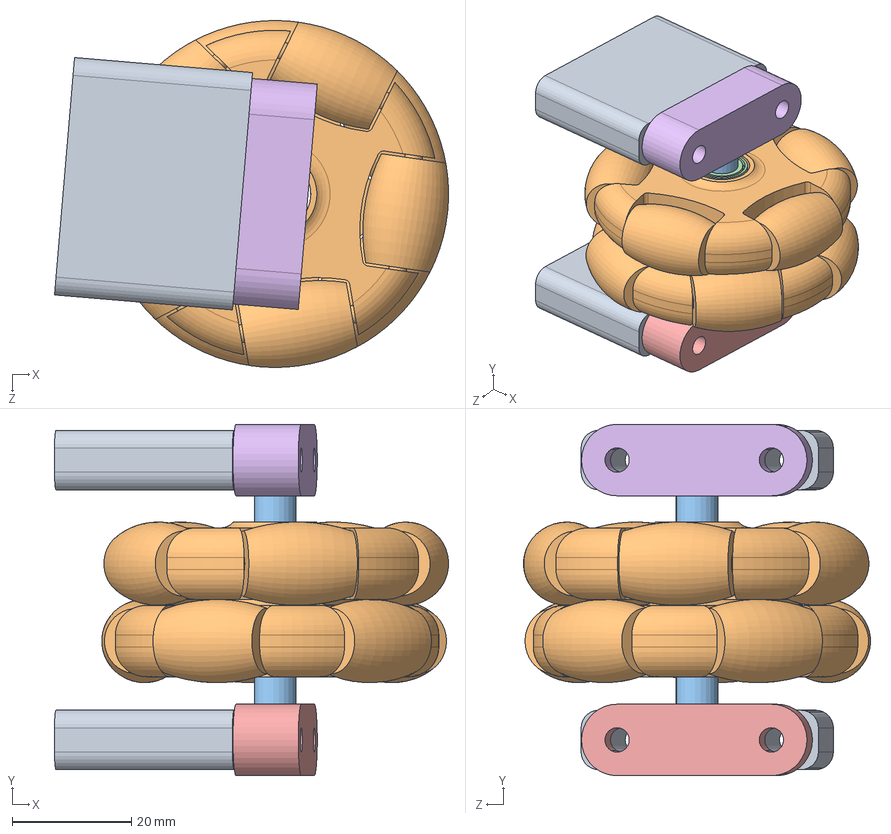
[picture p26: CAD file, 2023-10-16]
0.Model/装配体-支撑腿.SLDASM
66.2 x 59.0 x 58.3 mm
万向轮支撑腿-分体式 x 2
全向轮-网上找的模型58mm
全向轮光轴
全向轮轴承 x 2
全向轮轴座-键
全向轮轴座-圆

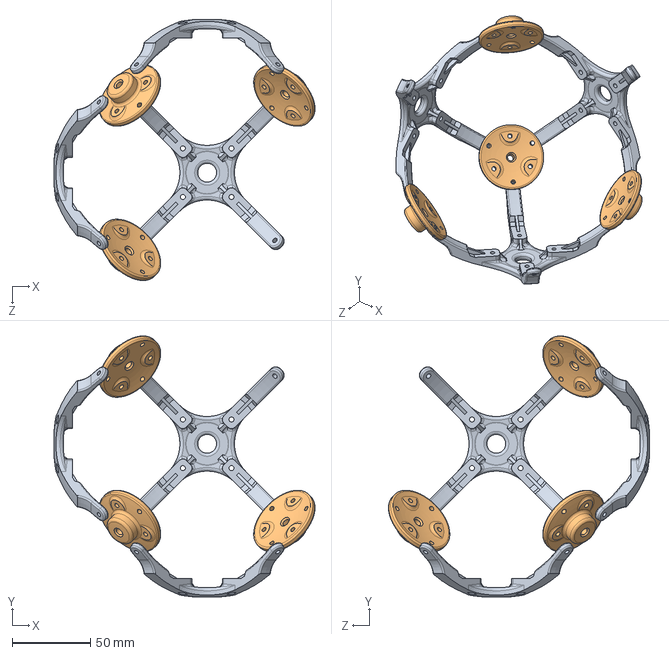
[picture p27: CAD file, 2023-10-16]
0.Model/总装配体-半边.SLDASM
166.4 x 166.4 x 166.4 mm
内部支撑架-连点 x 3
内部支撑架-桥接点 x 4

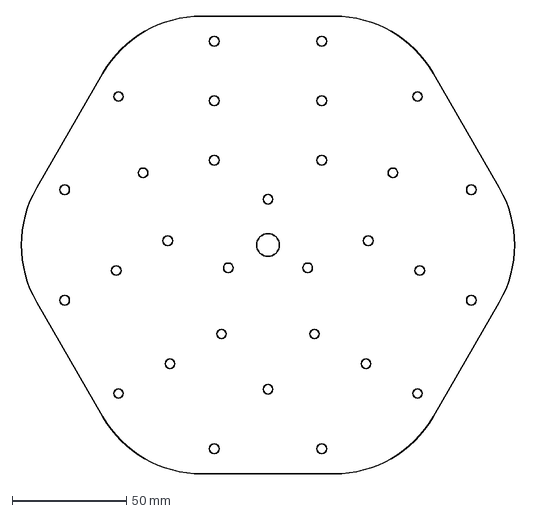
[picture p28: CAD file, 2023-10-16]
0.Model/3D打印/底盘-上层.DXF
219.9 x 200.0 mm

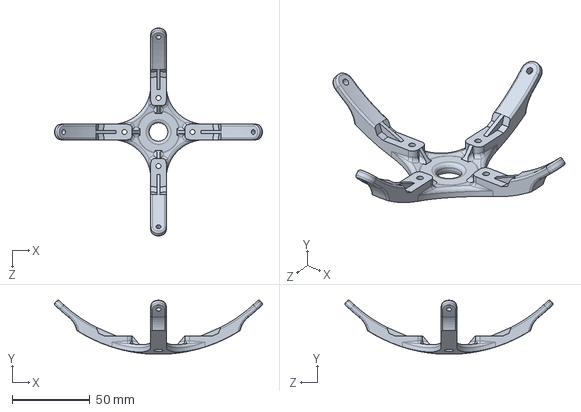
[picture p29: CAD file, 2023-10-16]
0.Model/内部/内部支撑架-连点.SLDPRT
134.0 x 34.6 x 134.0 mm

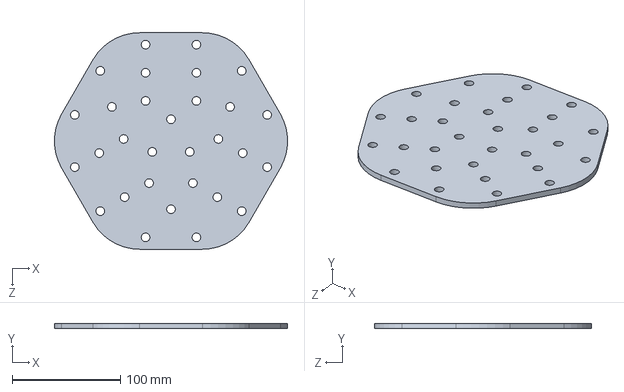
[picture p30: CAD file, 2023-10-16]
0.Model/底座/底盘-下层.SLDPRT
215.2 x 5.00 x 200.0 mm

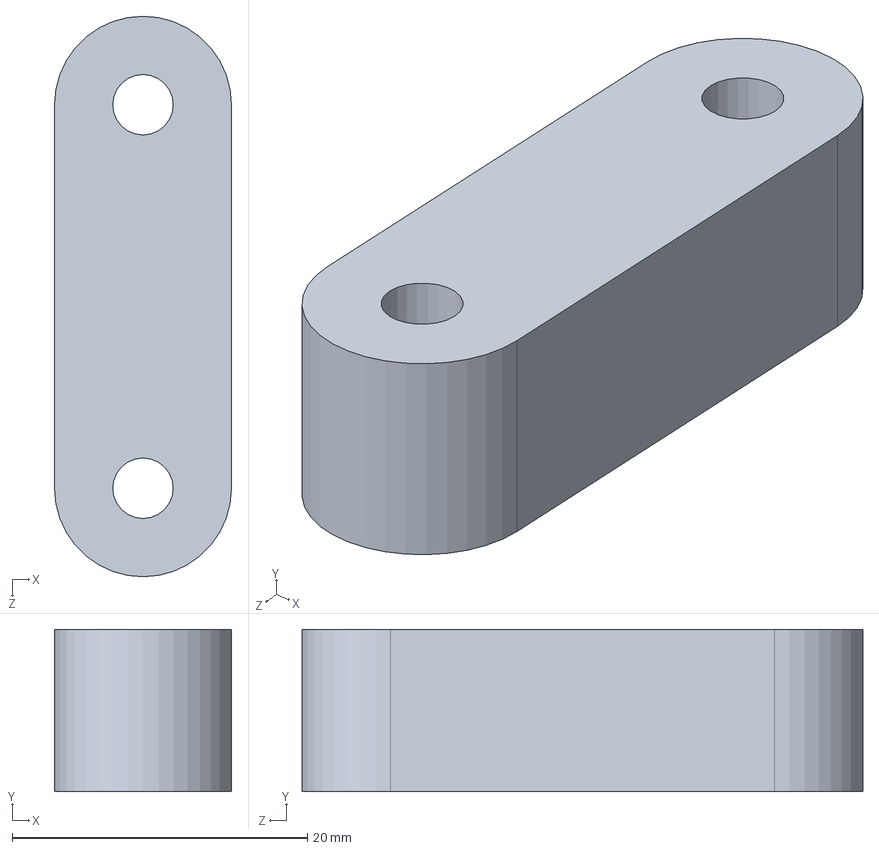
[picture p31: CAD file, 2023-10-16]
0.Model/底座/灰全向轮/全向轮轴座-键-6.SLDPRT
12.0 x 11.0 x 38.0 mm

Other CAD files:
0.Model/执行器/飞轮-80mm.SLDPRT
0.Model/整活/铁幕.STEP
0.Model/球壳/半球壳-直径200.SLDPRT
0.Model/电气/编码器板.SLDPRT
0.Model/3D打印/万向轮支撑腿-分体式.STL
0.Model/3D打印/全向轮轴座-圆.STL
0.Model/3D打印/全向轮轴座-圆6.STL
0.Model/3D打印/全向轮轴座-键-6.STL
0.Model/3D打印/全向轮轴座-键.STL
0.Model/内部/m3铜柱-主控板.SLDPRT
0.Model/内部/m3铜柱-电池.SLDPRT
0.Model/内部/内部支撑架-桥接点.SLDPRT
0.Model/内部/支架-电池小.SLDPRT
0.Model/内部/球壳示意.SLDPRT
0.Model/底座/万向轮支撑腿-分体式.SLDPRT
0.Model/底座/全向轮-网上找的模型58mm.SLDPRT
0.Model/底座/全向轮.SLDPRT
0.Model/底座/全向轮光轴.SLDPRT
0.Model/底座/全向轮轴座-圆.SLDPRT
0.Model/底座/全向轮轴座-键.SLDPRT
0.Model/底座/全向轮轴承.SLDPRT
0.Model/底座/底盘-上层.SLDPRT
0.Model/底座/灰全向轮/全向轮轴座-圆6.SLDPRT
0.Model/底座/灰全向轮/轴挡圈-6.SLDPRT
0.Model/底座/轴挡圈.SLDPRT
0.Model/执行器/m3铜柱-15mm.SLDPRT
0.Model/执行器/m3铜柱-4mm.SLDPRT
0.Model/执行器/电机-2804.SLDPRT
0.Model/执行器/电机轴.SLDPRT
0.Model/执行器/编码器板-AS5047P.SLDPRT
0.Model/执行器/飞轮-126mm.SLDPRT
0.Model/整活/苏联电厂.SLDPRT
0.Model/整活/苏联电厂.STEP
0.Model/整活/铁幕.SLDPRT
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

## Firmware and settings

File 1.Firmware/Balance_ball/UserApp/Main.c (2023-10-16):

//
// Created by 10798 on 2022/10/5.
//
#include <stdbool.h>
#include <tim.h>
#include <interface_can.h>
#include <attitude.h>
#include <utils/ctrl_math.h>
#include <icm20602.h>
#include <icm42688.h>
#include <interface_uart.h>
#include <retarget.h>
#include "common_inc.h"
#include "can.h"
#include "ctrl.h"
#include "ctrl_sin.h"

// 定义用哪个陀螺仪
enum IMU_CONFIG{
    IMU_USE_NONE,
    IMU_USE_ICM20602,
    IMU_USE_ICM42688P,
} imu_config;

uint16_t safe_time = 0;
/* Thread Definitions -----------------------------------------------------*/

/* Timer Callbacks -------------------------------------------------------*/


void HAL_TIM_PeriodElapsedCallback(TIM_HandleTypeDef *htim){
    //tim3定时器中断
    if (htim->Instance == TIM3) {

        //读取角速度和加速度
        if (imu_config == IMU_USE_ICM20602){
            icm20602AccAndGyroRead(&acc, &gyro);
            icm20602AccTransformUnit(&acc,&acc_f,&acc_drift);//转换单位
            icm20602GyroTransformUnit(&gyro,&gyro_f,&gyro_drift);//转换单位
        } else if(imu_config == IMU_USE_ICM42688P){
            icm42688AccAndGyroRead(&acc, &gyro);
            icm42688AccTransformUnit(&acc,&acc_f,&acc_drift);//转换单位
            icm42688GyroTransformUnit(&gyro,&gyro_f,&gyro_drift);//转换单位
        }

        //姿态解算
        //这里传入的参数坐标系有一个转换关系
        MahonyAHRSupdateIMU(q, gyro_f.x, gyro_f.y, gyro_f.z, acc_f.x, acc_f.y, acc_f.z);
        // 四元数反解欧拉角
        AttitudeQuaternionToEulerAngle(q,&state_attitude);
        // 转换单位
        AttitudeRadianToAngle(&state_attitude,&state_attitude_angle);

        //PID控制更新
        //更新当前姿态和目标姿态
        ////注意！！！在这里用的是弧度制
        CtrlStateUpdate(&gyro_f,&state_attitude,&ctrl_state);
        CtrlSetpointUpdate(&ctrl_rc, &ctrl_setpoint);
        //更新姿态控制pid
        CtrlUpdate(&ctrl_rc, &ctrl_state, &ctrl_setpoint, &ctrl_out);
        //更新飞轮转速到驱动板
        DriverSpeedUpdate(&ctrl_rc, &ctrl_out,&ctrl_out_sum, &motorSpeed);

        //添加安全保护，如果一定时间内没有收到串口的数据，则停车
        safe_time++;
        if (safe_time >= 100){
            ctrl_rc.armed = RC_ARMED_NO;
            HAL_GPIO_WritePin(RGB_G_GPIO_Port,RGB_G_Pin,GPIO_PIN_RESET);
            safe_time = 100;
        }

        DriverCmdSend(&ctrl_rc, &motorSpeed);

        //更新CTRL forward模式的时间
        ctrl_time += 10;
        if(ctrl_time > period){
            ctrl_time = 0;
        }
    }
}

/* UART Callbacks -------------------------------------------------------*/
//空闲中断在这里进行处理
void HAL_UARTEx_RxEventCallback(UART_HandleTypeDef *huart, uint16_t Size)
{
    if(huart->Instance==USART2)
    {
        //串口dma+空闲中断，接受wifi的指令
        WIFIRead(wifi_rx_buffer, &ctrl_rc);

        //如果正常收到了串口指令，则安全计时会一直清零
        safe_time = 0;
        HAL_GPIO_WritePin(RGB_G_GPIO_Port,RGB_G_Pin,GPIO_PIN_SET);
        //重新打开DMA接收 idle中断
        HAL_UARTEx_ReceiveToIdle_DMA(&WIFI_UART, wifi_rx_buffer, sizeof(wifi_rx_buffer));
    }
}

/* Default Entry -------------------------------------------------------*/
void Main(void) {
    //！！！
    //NOTE:注意！！！printf已经重定向到WIFI，gh 3p 的那个串口目前没用
    //！！！
    RetargetInit(&WIFI_UART);

    //陀螺仪自检
    HAL_Delay(1000);
    imu_config = IMU_USE_NONE;
    if (!icm20602_self_check()){
        imu_config = IMU_USE_ICM20602;
    } else if (!icm42688_self_check()){
        imu_config = IMU_USE_ICM42688P;
    }

    //陀螺仪初始化
    if (imu_config == IMU_USE_ICM20602){
        //init icm20602 and  calibrate
        icm20602Init();
        HAL_Delay(100);
        ICM20602_Gyro_And_Acc_Calibrate(&gyro_drift, &acc_drift);
    } else if(imu_config == IMU_USE_ICM42688P){
        icm42688Init();
        HAL_Delay(100);
        ICM42688P_Gyro_And_Acc_Calibrate(&gyro_drift, &acc_drift);
    }

    HAL_Delay(100);
    //初始化电机
    Drive_Clear_Error(M0);
    Drive_Clear_Error(M1);
    Drive_Clear_Error(M2);
    Drive_Init(M0);
    Drive_Init(M1);
    Drive_Init(M2);

    //PID
    CtrlPIDInit();

    //wifi 串口DMA空闲中断 enable
    HAL_UARTEx_ReceiveToIdle_DMA(&WIFI_UART, wifi_rx_buffer, sizeof(wifi_rx_buffer));

    //启动定时器
    HAL_TIM_Base_Start_IT(&htim3);

    while (1){

        // Check for UART errors and restart recieve DMA transfer if required
        if (WIFI_UART.ErrorCode != HAL_UART_ERROR_NONE)
        {
            HAL_UART_AbortReceive(&WIFI_UART);
            HAL_UARTEx_ReceiveToIdle_DMA(&WIFI_UART, wifi_rx_buffer, sizeof(wifi_rx_buffer));
        }

        //----------------------------------------wifi通信发送-----------------------------------

        //TODO：实时给上位机发送自身姿态数据，包括四元数与欧拉角，printf逗号隔开即可
        //TODO：上位机写一个pygame虚拟游戏手柄，用来自稳模式玩赛车游戏

        //-------------------------------------------------------------------------------------

//        printf("%.3f,%.3f,%.3f\r\n", motorSpeed.m1, motorSpeed.m2, motorSpeed.m3);
        printf("%.3f,%.3f,%.3f\r\n", state_attitude_angle.roll, state_attitude_angle.pitch, state_attitude_angle.yaw);
//        printf("%.3f,%.3f,%.3f,%.3f,%.3f,%.3f\r\n",gyro_f.x,gyro_f.y,gyro_f.z,acc_f.x,acc_f.y,acc_f.z);
//        printf("Hello World!\r\n");

        //Blink
        HAL_GPIO_TogglePin(RGB_B_GPIO_Port,RGB_B_Pin);
        //-----------------------------Delay
        HAL_Delay(100);
    }
}

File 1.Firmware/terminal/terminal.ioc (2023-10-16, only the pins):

Mcu.UserName=STM32F103C8Tx
PA11.GPIO_Label=KEY2
PA11.Signal=GPIO_Input
PA12.GPIO_Label=KEY1
PA12.Signal=GPIO_Input
PA13.Signal=SYS_JTMS-SWDIO
PA14.Signal=SYS_JTCK-SWCLK
PA2.Signal=USART2_TX
PA3.Signal=USART2_RX
PA4.Signal=ADCx_IN4
PB10.Signal=I2C2_SCL
PB11.Signal=I2C2_SDA
PB12.GPIO_Label=OLED_DC
PB12.Signal=GPIO_Output
PB13.Signal=SPI2_SCK
PB14.GPIO_Label=OLED_RST
PB14.Signal=GPIO_Output
PB15.Signal=SPI2_MOSI
PC13-TAMPER-RTC.GPIO_Label=LED0
PC13-TAMPER-RTC.Signal=GPIO_Output
PD0-OSC_IN.Signal=RCC_OSC_IN
PD1-OSC_OUT.Signal=RCC_OSC_OUT

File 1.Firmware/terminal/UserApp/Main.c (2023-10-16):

#include <attitude.h>
#include "common_inc.h"
#include "usart.h"

#include "mpu6050.h"
#include "ctrl_types.h"
#include <oled.h>
#include <stm32f1xx_hal_tim.h>
#include <menu.h>
#include <multi_button.h>
#include <tim.h>
#include "retarget.h"

ctrl_rc_t terminal_rc;
struct Button button1;
struct Button button2;

uint16_t mytime = 0;

#define WIFI_BUFFER_LENGTH     16
uint8_t wifi_tx_buffer[WIFI_BUFFER_LENGTH];

/* Thread Definitions -----------------------------------------------------*/

/* Timer Callbacks -------------------------------------------------------*/
void HAL_TIM_PeriodElapsedCallback(TIM_HandleTypeDef *htim){
    //tim3定时器中断
    if (htim->Instance == TIM3) {
        //10ms
        //读取角速度和加速度
        mpu6050AccAndGyroRead(&acc, &gyro);
        mpu6050AccTransformUnit(&acc,&acc_f,&acc_drift);//转换单位
        mpu6050GyroTransformUnit(&gyro,&gyro_f,&gyro_drift);//转换单位

        //姿态解算
        //这里传入的参数坐标系有一个转换关系，源数据是东北天坐标系，抄的这个算法是北西天坐标系
        MahonyAHRSupdateIMU(q, gyro_f.x, gyro_f.y, gyro_f.z, acc_f.x, acc_f.y, acc_f.z);
        // 四元数反解欧拉角
        AttitudeQuaternionToEulerAngle(q,&state_attitude);
        // 转换单位
        AttitudeRadianToAngle(&state_attitude,&state_attitude_angle);

        //注意这里现在是  弧度制
        terminal_rc.roll = state_attitude.roll;
        terminal_rc.pitch = state_attitude.pitch;
        terminal_rc.yaw = state_attitude.yaw;

        mytime++;
//        printf("%.3f,%.3f,%.3f,%.3f\r\n",state_attitude_angle.roll,state_attitude_angle.pitch,state_attitude_angle.yaw,(float)mytime);


    } else if (htim->Instance == TIM4) {
        //5ms
        //按键扫描
        button_ticks();
    }  else if (htim->Instance == TIM2) {
        //50ms
        //wifi发送数据
        memcpy(&wifi_tx_buffer[0], &terminal_rc.armed, sizeof(uint16_t));
        memcpy(&wifi_tx_buffer[2], &terminal_rc.mode, sizeof(uint16_t));
        memcpy(&wifi_tx_buffer[4], &terminal_rc.roll, sizeof(float));
        memcpy(&wifi_tx_buffer[8], &terminal_rc.pitch, sizeof(float));
        memcpy(&wifi_tx_buffer[12], &terminal_rc.yaw, sizeof(float));
        HAL_UART_Transmit(&WIFI_UART, wifi_tx_buffer,sizeof(wifi_tx_buffer),0xffff);
    }


}

//软件定时器虽好，可不要贪杯欧

/* Default Entry -------------------------------------------------------*/
void Main(void) {
    RetargetInit(&WIFI_UART);

    oled_init();

    //init mpu6050
    mpu6050Init();
    HAL_Delay(1000);
    Gyro_And_Acc_Calibrate(&gyro_drift, &acc_drift);

    ////==========================按键相关===========================================
    // 初始化按键（硬件相关）
    button_init(&button1, read_button_GPIO, 0,1);
    button_init(&button2, read_button_GPIO, 0,2);
    // 按键回调函数（软件相关）
    // arm按钮
    button_attach(&button1, SINGLE_CLICK,     BTN_SINGLE_Click_Handler);
    button_attach(&button1, LONG_PRESS_START,     BTN_LONG_Press_Start_Handler);
    // mode按钮
    button_attach(&button2, SINGLE_CLICK,     BTN_SINGLE_Click_Handler);
    button_attach(&button2, LONG_PRESS_START,     BTN_LONG_Press_Start_Handler);
    //打开btn
    button_start(&button1);
    button_start(&button2);

    //初始化遥控状态
    terminal_rc.roll = 0.0f;
    terminal_rc.pitch = 0.0f;
    terminal_rc.yaw = 0.0f;
    terminal_rc.armed = RC_ARMED_NO;
    terminal_rc.mode = RC_MODE_STABILIZED;

    //启动定时器
    HAL_TIM_Base_Start_IT(&htim2);
    HAL_TIM_Base_Start_IT(&htim3);
    HAL_TIM_Base_Start_IT(&htim4);

    while (1){
        ////=====================================================================
        //oled显图
        oled_show_string( 0, 2, "ROLL:");
        oled_show_string( 0, 4, "PITCH:");
        oled_show_string( 0, 6, "YAW:");

        oled_show_float( 48, 0, (float) mytime,4,0);
        oled_show_float( 60, 2, state_attitude_angle.roll,3,2);
        oled_show_float( 60, 4, state_attitude_angle.pitch,3,2);
        oled_show_float( 60, 6, state_attitude_angle.yaw,3,2);

        if(terminal_rc.armed == RC_ARMED_NO)
            oled_show_string( 0, 0, "DIS");
        else if(terminal_rc.armed == RC_ARMED_YES)
            oled_show_string( 0, 0, "ARM");

        if(terminal_rc.mode == RC_MODE_STABILIZED)
            oled_show_string( 100, 0, "STB");
        else if(terminal_rc.mode == RC_MODE_POSITION)
            oled_show_string( 100, 0, "POS");
        else if(terminal_rc.mode == RC_MODE_FORWARD)
            oled_show_string( 100, 0, "FWD");

        HAL_GPIO_TogglePin(LED0_GPIO_Port,LED0_Pin);

        HAL_Delay(10);
    }
}

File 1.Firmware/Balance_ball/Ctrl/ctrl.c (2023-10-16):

//
// Created by 10798 on 2022/12/14.
//

#include "ctrl.h"
#include "pid.h"
#include "utils/ctrl_math.h"

#include <math.h>
#include <interface_can.h>
#include "tim.h"
#include "ctrl_types.h"
#include "senser_types.h"
#include "ctrl_sin.h"

//TODO:增加这几个东西的初始化函数
float ctrl_time = 0;
ctrl_rc_t ctrl_rc;
ctrl_state_t ctrl_state;
ctrl_setpoint_t ctrl_setpoint;
ctrl_setpoint_t ctrl_setpoint_offboard;
ctrl_out_t ctrl_out;
ctrl_out_t ctrl_out_sum;
motorSpeed_t motorSpeed = {0.0f, 0.0f, 0.0f};

//PID
pid_calc_t roll_pid;
pid_calc_t pitch_pid;
pid_calc_t yaw_pid;
pid_calc_t rollRate_pid;
pid_calc_t pitchRate_pid;
pid_calc_t yawRate_pid;

float damp_vel = 0.8f;
float damp_deadzone = 10.0f;

void CtrlPIDInit(void){
    //初始化PID
    //外环 注意现在是弧度值
    PID_init(&roll_pid, PID_POSITION, 5.0f,0,0, 100,0);
    PID_init(&pitch_pid, PID_POSITION, 5.0f,0,0, 100,0);
    PID_init(&yaw_pid, PID_POSITION, 5.0f,0,0, 100,0);
    //内环 不要d，因为角速度本来就很抖
    PID_init(&rollRate_pid, PID_POSITION, 20.0f,0,0, 100,0);
    PID_init(&pitchRate_pid, PID_POSITION, 20.0f,0,0, 100,0);
    PID_init(&yawRate_pid, PID_POSITION, 20.0f,0,0, 100,0);
}

void CtrlStateUpdate(const Axis3f* _gyro_f, const attitude_t* _attitude, ctrl_state_t* _state){
    //通过姿态解算获得的实际值，存在state里，无需进行单位换算
    //TODO:到这里应该是正负都已经弄好的,如果不对记得看看
    _state->attitudeRate.roll = _gyro_f->x;
    _state->attitudeRate.pitch = _gyro_f->y;
    _state->attitudeRate.yaw = _gyro_f->z;

    ////注意！！！在这里用的是弧度制
    _state->attitude.roll = _attitude->roll;
    _state->attitude.pitch = _attitude->pitch;
    _state->attitude.yaw = _attitude->yaw;
}


void CtrlSetpointUpdate(const ctrl_rc_t* _rc, ctrl_setpoint_t* _setpoint){
    // 通过rc获得期望值，存在setpoint里
    if(_rc->mode == RC_MODE_STABILIZED) //自稳模式
    {
        //期望角速度
        _setpoint->attitudeRate.roll = 0;
        _setpoint->attitudeRate.pitch = 0;
        _setpoint->attitudeRate.yaw = 0;
    }
    else if(_rc->mode == RC_MODE_POSITION) //定姿模式
    {
        // 期望角度
        _setpoint->attitude.roll = _rc->roll;
        _setpoint->attitude.pitch = _rc->pitch;
        _setpoint->attitude.yaw = _rc->yaw;
    }
    else if(_rc->mode == RC_MODE_DEV) //开环前向模式
    {
        _setpoint->attitude.roll = _rc->roll;
        _setpoint->attitude.pitch = _rc->pitch;
        _setpoint->attitude.yaw = _rc->yaw;
    }
    else
    {
        //什么mode都没识别到，按自稳的给，全给0
        _setpoint->attitude.roll = 0;
        _setpoint->attitude.pitch = 0;
        _setpoint->attitude.yaw = 0;
        _setpoint->attitudeRate.roll = 0;
        _setpoint->attitudeRate.pitch = 0;
        _setpoint->attitudeRate.yaw = 0;
    }

}


void CtrlUpdate(const ctrl_rc_t* _rc, const ctrl_state_t* _state, ctrl_setpoint_t* _setpoint, ctrl_out_t* _out){
    //先判断是否解锁
    if(_rc->armed == RC_ARMED_YES){

        if(_rc->mode == RC_MODE_STABILIZED) //自稳模式
        {
            //只算内环角速度环
            _out->roll =  PID_calc(&rollRate_pid, _state->attitudeRate.roll, _setpoint->attitudeRate.roll);
            _out->pitch = PID_calc(&pitchRate_pid, _state->attitudeRate.pitch, _setpoint->attitudeRate.pitch);
            _out->yaw = PID_calc(&yawRate_pid, _state->attitudeRate.yaw, _setpoint->attitudeRate.yaw);

        }
        else if(_rc->mode == RC_MODE_POSITION) //定姿模式
        {
            //连PID都没有
            _out->roll =  _setpoint->attitude.roll;
            _out->pitch = _setpoint->attitude.pitch;
            _out->yaw =  _setpoint->attitude.yaw;

            _out->roll = scaleRangef(_out->roll, -1, 1, -30, 30);
            _out->pitch = scaleRangef(_out->pitch, -1, 1, -30, 30);
            _out->yaw = scaleRangef(_out->yaw, -1, 1, -30, 30);

        }
        else if(_rc->mode == RC_MODE_DEV) //开发者模式
        {
            if( fabsf(_state->attitude.roll - _setpoint->attitude.roll) <= 0.1){ //弧度值
                _setpoint->attitude.roll = _state->attitude.roll;
            }
            if( fabsf(_state->attitude.pitch - _setpoint->attitude.pitch) <= 0.1){
                _setpoint->attitude.pitch = _state->attitude.pitch;
            }
            if( fabsf(_state->attitude.yaw - _setpoint->attitude.yaw) <= 0.1){
                _setpoint->attitude.yaw = _state->attitude.yaw;
            }

            ////------------------------------------------普通串级环-----------------------------------------------------////
            //先算外环pid
            _setpoint->attitudeRate.roll = PID_calc(&roll_pid, _state->attitude.roll, _setpoint->attitude.roll);
            _setpoint->attitudeRate.pitch = PID_calc(&pitch_pid, _state->attitude.pitch, _setpoint->attitude.pitch);
            _setpoint->attitudeRate.yaw = PID_calc(&yaw_pid, _state->attitude.yaw, _setpoint->attitude.yaw);
            //再算内环pid
            _out->roll =  PID_calc(&rollRate_pid, _state->attitudeRate.roll, _setpoint->attitudeRate.roll);
            _out->pitch = PID_calc(&pitchRate_pid, _state->attitudeRate.pitch, _setpoint->attitudeRate.pitch);
            _out->yaw = PID_calc(&yawRate_pid, _state->attitudeRate.yaw, _setpoint->attitudeRate.yaw);
        }
        else
        {
            //什么mode都没识别到，全给0
            _out->roll = 0;
            _out->pitch = 0;
            _out->yaw = 0;
        }

    }
    else {
        //没解锁
        _out->roll = 0;
        _out->pitch = 0;
        _out->yaw = 0;
    }
}
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

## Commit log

2023-10-16 init
    init
    [m3铜柱-15mm.SLDPRT, m3铜柱-4mm.SLDPRT, m3铜柱-主控板.SLDPRT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]
2023-10-16 change
    change
    [m3铜柱-15mm.SLDPRT, m3铜柱-4mm.SLDPRT, m3铜柱-主控板.SLDPRT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]
